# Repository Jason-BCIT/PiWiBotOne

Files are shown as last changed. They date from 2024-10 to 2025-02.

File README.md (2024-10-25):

The PiWiBot is a small, mobile, educational robot using the Raspberry Pi Pico microcontroller board.
The original code and inspiration for the software was developed and shared by Adrian Cruceru as "crawlspacebot". https://github.com/AdrianCX/crawlspacebot 

The printed circuit board is available from PCBWAY at https://www.pcbway.com/project/shareproject/PiWiBot_One_51645550.html 
Or you can manufacture your own, single sided board using the files included here.

To see two PiWiBots playing: https://youtu.be/jH2G25Dmx2Y  

To view the CAD in native Fusion 360 format: https://a360.co/40o5nz3 

The board is compatible with the "Tethered Mini Sumo" project.. a common "Tech Studies" project in British Columbia. https://botshop.wordpress.com/2011/03/30/tethered-mini-sumo-robots/ 
The entire robot, as presented here, can be manufactured for approximately $20CAD (batteries not included!) as of October 2024

To install the software, install Thonny on your computer and use it to copy the MicroPython image to your Raspberry Pi Pico W, using the instructions here: https://projects.raspberrypi.org/en/projects/getting-started-with-the-pico/2 

Copy the code in the Code folder to a folder on your computer. Open the code in Thonny, and then save to the Pico W.

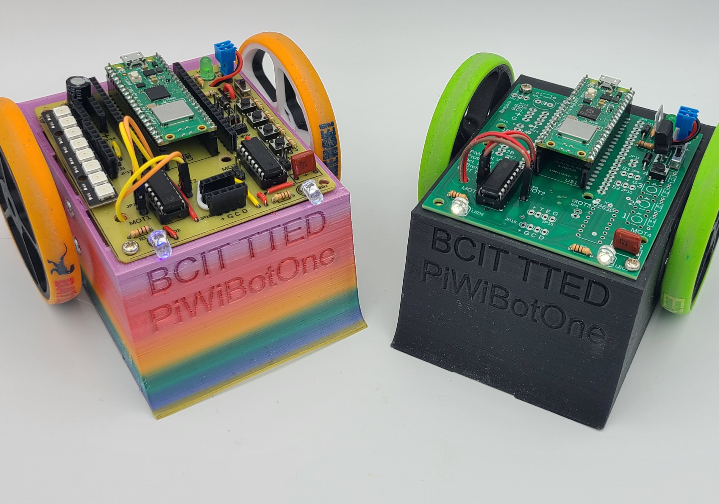
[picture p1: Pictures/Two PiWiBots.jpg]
Two PiWiBots


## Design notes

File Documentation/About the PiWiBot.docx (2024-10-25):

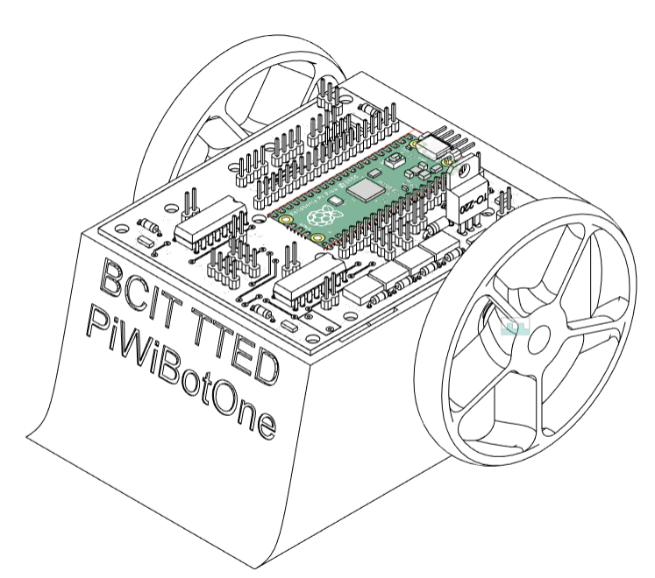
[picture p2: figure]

The $20 PiWiBot

(Raspberry Pi Pico Wireless Robot)

John Pinto wanted to make his tethered mini sumo robots wireless… for $20 or less (batteries not included.) The $8.00 Raspberry Pi Pico W board made this possible!

Contact: Jason Brett jbrett@bcit.ca

Give it a try!

PiWiBot Minimal Parts List | Vendor | Price
Raspberry Pi Pico W | Canakit | $8.00
L293D Motor driver | Amazon | $1.00
2 x TT Motor Gearbox | Amazon | $3.50
1 SPDT Slide Switch | Amazon | $0.13
3 x LEDs | Any | $0.30
2 x Rectifier Diodes | Any | $0.20
4 x resistors (2x100, 470,10K) | Any | $0.04
2 x 20pin header sockets | Lee’s | $0.90
2 x 40pin header pins | Lee’s | $1.00
1 x 180nF (approx.) cap | Any | $0.30
2 x Silicone Wrist Bands | Amazon | $1.00
113g PLA filament | Any | $2.60
1 x 4AA Battery Pack | Lee’s | $1.00
2 x Nut Inserts for 3D prints | Amazon | $0.25
2 x 3mm x 6mm screws | Any | $0.25
1 x Printed Circuit Board | PCBWAY | $1.80
Total Entry Level Price | | $22.27

And, technically you could get rid of the headers, solder the Pico directly to the board, screw directly to the plastic and hit the $20 price point. (Batteries not included, of course!)

1) Turn the switch (by the green power LED) ON.
2) Connect to:
  a. “PiWiBotOne” for the Rainbow Robot
  b. “PiWiBotTwo” for the Black Robot
  c. Password is “123456789”
  d. Navigate your browser to 192.168.4.1
3) Drive robot with left hand joystick. Use red corner buttons to control LEDs.
  a. The slider is for servo control, and the other joystick is for extra motors.
    i. The PiWiBot supports up to four DC motors and two servo motors.
4) The Rainbow bot has a 120:1 gearbox, the Black Robot has a 48:1 gearbox.
5) Remember to turn the robot off when done, please!

About the board:

1) The Rainbow bot’s board was made in the shop… good for one-off and prototypes
  a. The Black bot’s board was made by PCBWAY… $1.80 each in quantity of 100.
    i. Want to build a PiWiBot? Ask me for a sample board!
2) The code is mostly MicroPython, with Javascript and HTML used to create the web page.
  a. I’m happy to share… it is plug and play. (Mostly… but PC/Mac/Linux compatible)
  b. Lots of development left to go for additional accessories.
    i. Line following / edge detecting
    ii. Range finding with Ultrasonic or LIDAR rangefinders
    iii. OLED display on board
    iv. Speaker (apparently the Pico can play MP3 files… but I haven’t figured that out yet.)
    v. Multiple pushbuttons
    vi. Anything you want because you can add an expansion board using headers!
      1. I do plan to have a series of Youtube videos and explanations… one day.
3) You can power the robot using any 5V-12V battery. (I’m using 4xAA… Alkaline or NiMh)
4) This robot uses the “TT Motor Gearbox” but the Tamiya gearboxes will work fine, too.

This board is fully compatible with the standard tethered mini sumo robot project. It simply replaces the control board. It has two wires for the battery and two wires for each motor, just like the tethered board!

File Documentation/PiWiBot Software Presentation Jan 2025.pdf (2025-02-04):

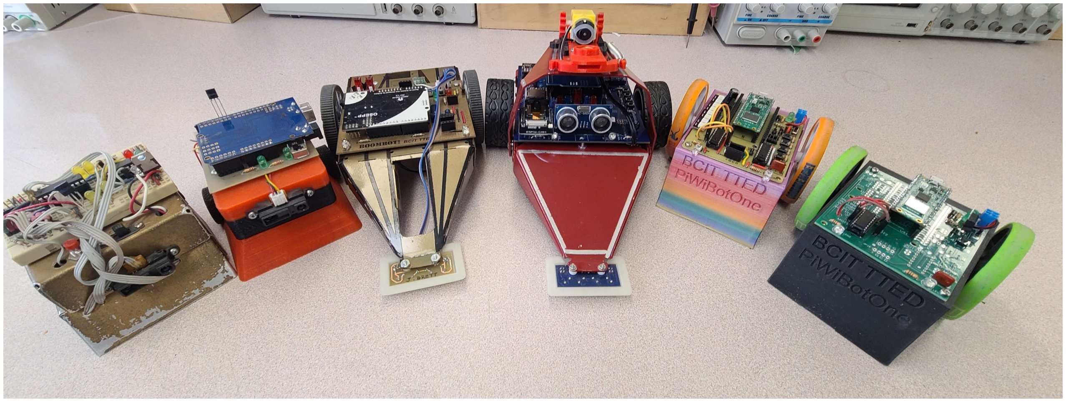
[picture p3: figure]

# PiWiBot Software

How I think it works.

Jason Brett
BCIT TTED
January 2025

# Coded in MicroPython

## - An Interpreted Language:

### - The PicoW doesn’t “run your code”

- It runs a “MicroPython Interpreter”

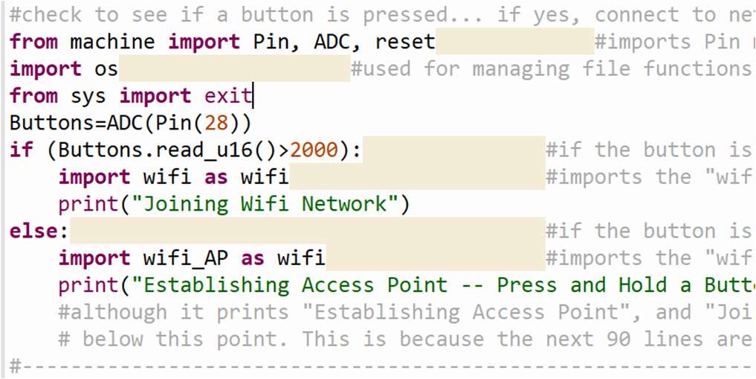
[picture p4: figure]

- Your source code is stored on the PicoW and executed one command at a time
- Use “Thonny” to install the MicroPython interpreter • Then to upload your code to the PicoW

## - On PicoW boot up the Micropython Interpreter starts to run

### - It looks for a file called “main.py”

- It executes the first instruction in that file
- Then the next, etc.

# Different from the Arduino IDE

## - Arduino IDE:

- Compiled language (“C++”) • Your computer converts your

source code to machine language instructions

### - The code on the microcontroller is in machine code

- You can’t read it or change it • You have to re-compile and re-

download

### - Benefit: Compiled code runs faster than interpreted

- (as a general rule)

## - Micropython:

- Interpreted language (“Python”) • Your microcontroller stores, reads

and executes source code

### - The code on the microcontroller is in source code

- You can edit and change it easily
- No need to re-compile or re-download

### - Benefit: Interpreted code can be easier to develop

- Faster chips compensate for slower code

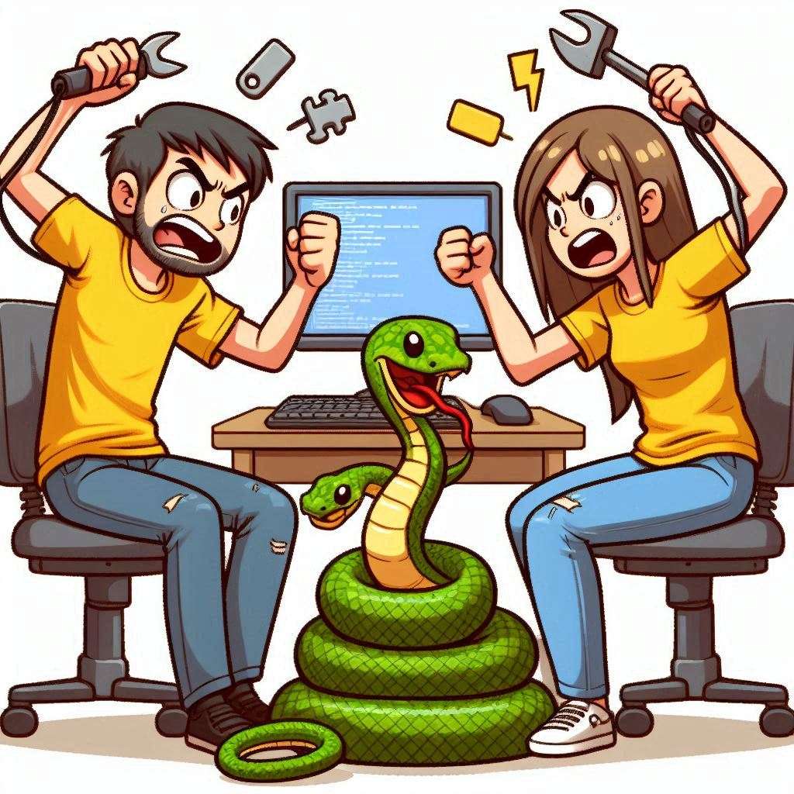
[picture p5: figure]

# Notable Syntax Differences

## - Python does not require semi-colons at end of line - Python does not use {loop} to manage loops

### - Loops are managed by indentations

- Indentation really, really matters!

## - Python’s comment code is “#” rather than “//” - “print()” includes the line feed and carriage return

### - “println()” not needed

## - Python offers several benefits when managing data

### - Not so important in this application but can reduce coding time

“A cartoon image of two computer programmers, one male, one female, fighting with a Python.” Generated by Microsoft CoPilot, Feb 2025

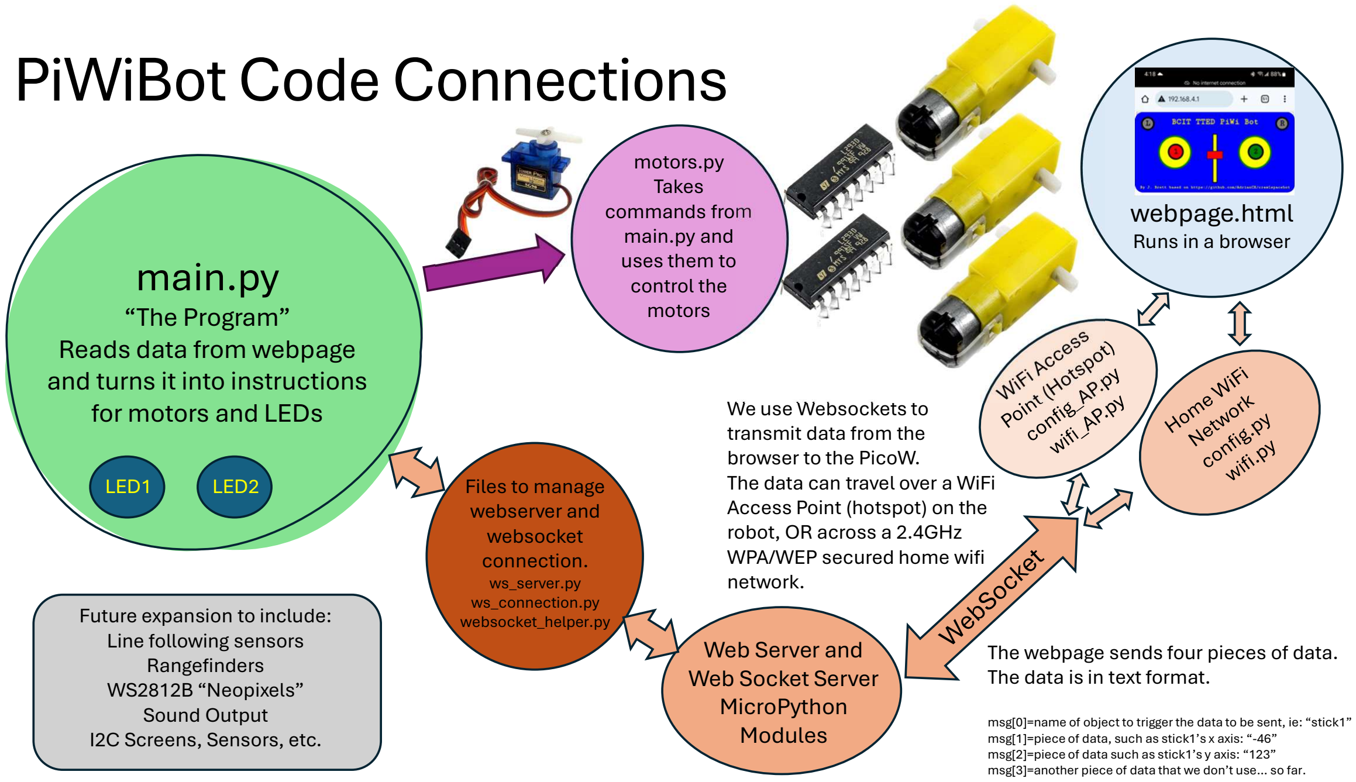
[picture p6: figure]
PiWiBot Code Connections; webpage.html Runs in a browser; Web Server and Web Socket Server MicroPython Modules; We use Websockets to transmit data from the browser to the PicoW. The data can travel over a WiFi Access Point (hotspot) on the robot, OR across a 2.4GHz WPA/WEP secured home wifi network.; The webpage sends four pieces of data. The data is in text format.; Files to manage webserver and websocket connection. ws_server.py ws_connection.py websocket_helper.py; main.py; “The Program” Reads data from webpage and turns it into instructions for motors and LEDs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

msg[0]=name of object to trigger the data to be sent, ie: “stick1” msg[1]=piece of data, such as stick1’s x axis: “-46” msg[2]=piece of data such as stick1’s y axis: “123” msg[3]=another piece of data that we don’t use… so far.

# Change WiFi Details

## - Config.py

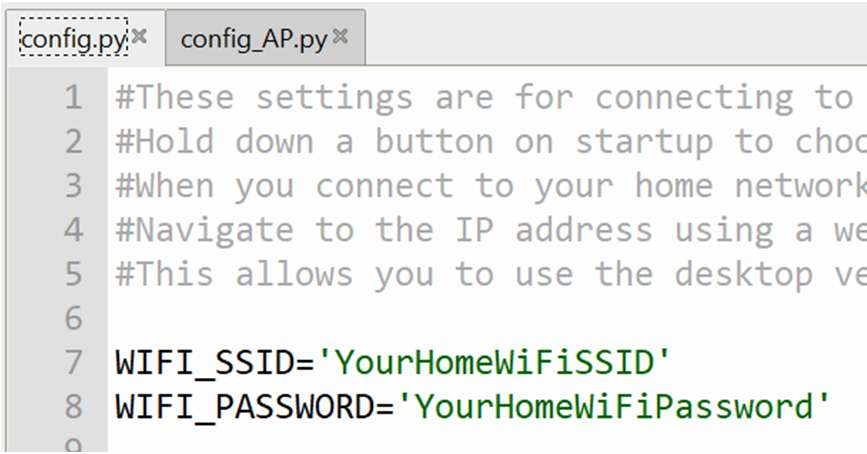
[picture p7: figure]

### - The SSID and Password for connecting to your home network - Hold down “the button” on the board on startup to connect

## - Config_AP.py

- Change the name of your robot’s network Access Point • Seriously, DO this… we don’t want six robot APs all named “PiWiBot”! • Add a password if you want.

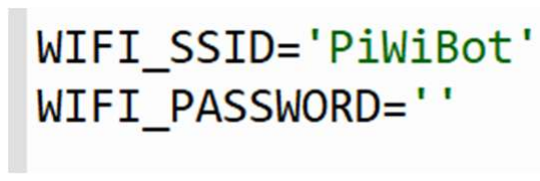
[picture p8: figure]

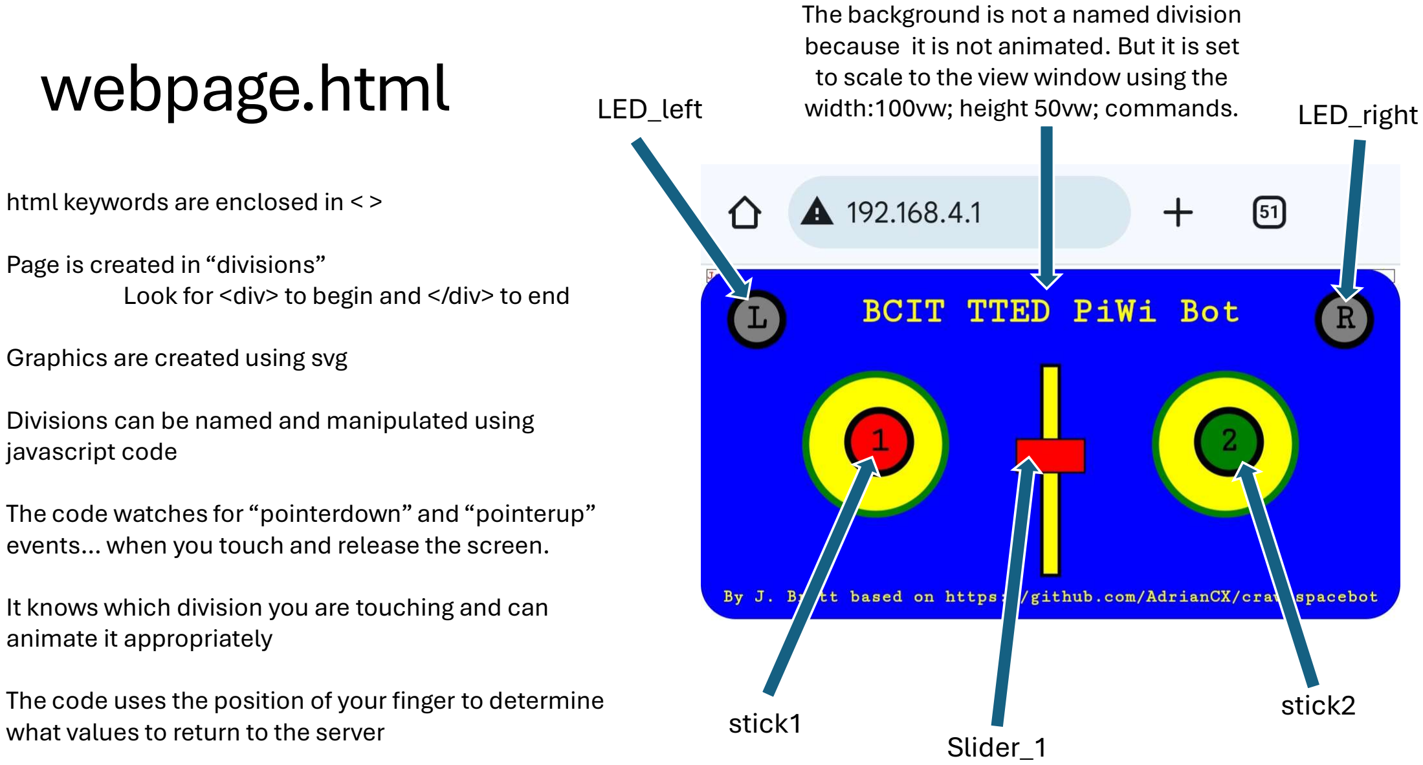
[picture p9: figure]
webpage.html; html keywords are enclosed in < >; Page is created in “divisions”; Graphics are created using svg; javascript code; animate it appropriately; what values to return to the server; LED_left; LED_right; stick1; stick2; Slider_1; The background is not a named division; to scale to the view window using the width:100vw; height 50vw; commands.

Look for <div> to begin and </div> to end

Divisions can be named and manipulated using

The code watches for “pointerdown” and “pointerup” events… when you touch and release the screen.

It knows which division you are touching and can

The code uses the position of your finger to determine because it is not animated. But it is set

# What Can I Hack?

## - Lots of easy stuff to change:

- Look for things between quotes… fill=“blue”, or r=“40”
- Look for text between <text> and </text> commands
- <text x="200" y="190" font-size="10" text-anchor="middle" fill="Yellow">By J. Brett based on https://github.com/AdrianCX/crawlspacebot</text>

## - A bit trickier, but you can remove unused objects

- Save a “webpage.backup” file in case you need to go back to step one!
- Delete the section from <div id=“stick2” to the next </div>
- At the end of the file delete the “let joystick2= ….,16); • Do the same for Slider1 if you don’t need it • Now can you re-centre joystick 1 to the middle of the screen?

## - Maybe you want one joystick with two sliders?

# How Does the Joystick Work?

- let joystick1 = new JoystickController("stick1", 128, 16); • Creates a new Joystick object • Names it “stick1”
- Associates it with the “stick1” division graphics
- The round button… it will animate this button as you move your thumb
- Creates a maximum range of movement of 128 drawing units
- Creates a “deadband” of 16 drawing units
- When either X or Y is less than 16 units from centre, it sets it to zero
- Makes it easier to re-centre the stick, and prevents accidental bumps

### - I was completely stuck on how to do this until I found

- “CrawlSpaceBot” by Adrian Cruceru on Github
- I’ve figured most of it out, but not all of it…. yet.

Y= -128

Y= +128

X= -128 | X= +128 Dead
Band

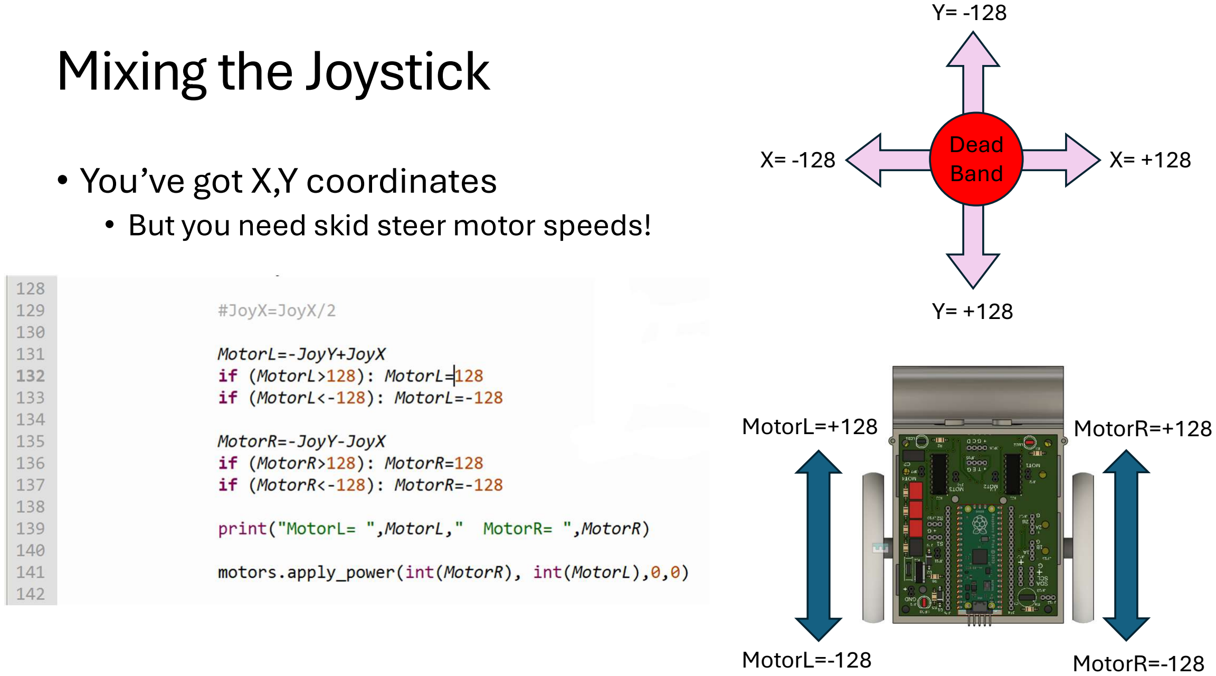
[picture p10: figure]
Mixing the Joystick; • You’ve got X,Y coordinates • But you need skid steer motor speeds!; X= +128 Dead; Band; MotorL=+128; MotorL=-128; MotorR=+128; MotorR=-128

# Driving the Motors

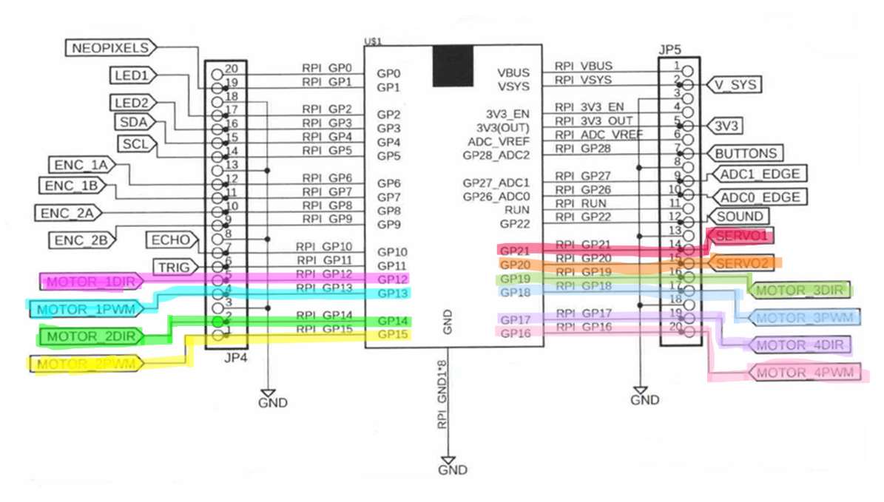
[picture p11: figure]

## - Wiring Determined by Schematic - Each motor has

### - 1 “DIR” pin to set direction - 1 “PWM” pin to set speed

- If decreasing the duty cycle makes the motor speed up going forward (DIR=HIGH) • Then increasing the duty cycle makes the motor speed up going in reverse (DIR=LOW)

## - Pico has many PWM options

- Set the frequency (how often it turns on and off) • We use a default of 5000Hz… you can sometimes hear a 5000Hz whining! • Set the duty cycle (the fraction of the time that it is turned “on”) • This is a fraction of a 16 bit number… 0 is “always off”, 65,535 is “always on”
- The Arduino only has an 8 bit “analogWrite”… at 980Hz

# Motors Need a Kickstart

## - The friction on the gearbox requires a minimum torque to turn

### - Below this the motor is stalled - The code uses a PWM setting of 25,000/65,536 = 38% to start up

- The code scales the motor response from 38% at low throttle to 100% at full throttle

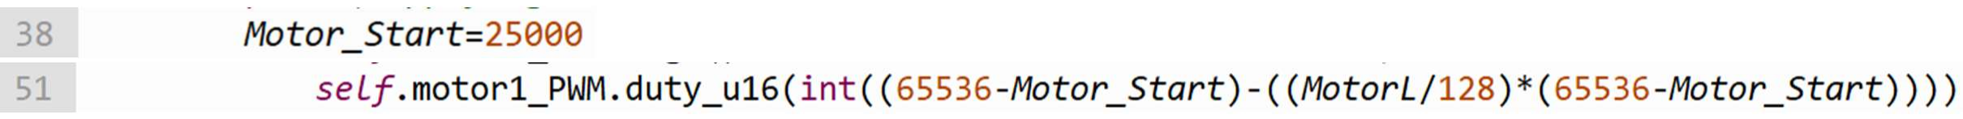
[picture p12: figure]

## - Often motors are “reversed”

### - Direction can be changed by swapping the wires on the board, or - Swapping a “+” to a “-” in code

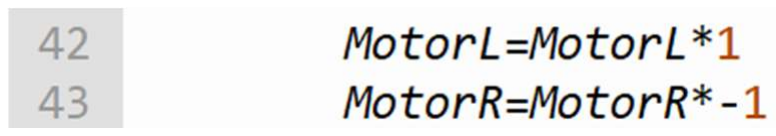
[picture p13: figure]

# Motor3 is On Slider1

### - You can slide the slider to position and leave it there

- You can take your thumb
off the controller and
Motor3 keeps moving
- It’s “return to zero”
function has been turned
off in the webpage
javascript code
- It won’t stop when you stop the code from Thonny
- You’ll need to add some
lines to shut the motor
down automatically
- Look at lines 168-174 in main.py

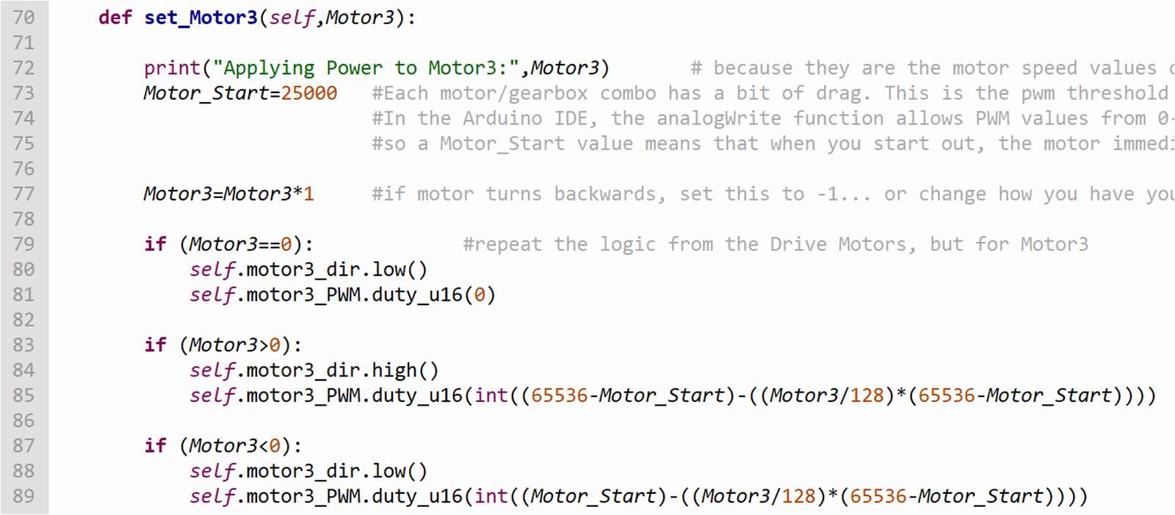
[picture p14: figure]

# Servo1 Uses Joystick2’s Y-Axis

## - We use a 50Hz PWM signal to send a pulse every 20ms

### - Servos will turn off if they don’t receive regular updates

## - Typical pulse lengths for a “hobby servo” are 1000-2000ms

- Neutral position is 1500ms (angle=0) • Positions range from +128 to -128 in our code

### - We set the duty cycle using nanoseconds

- 1500ms = 1,500,000ns

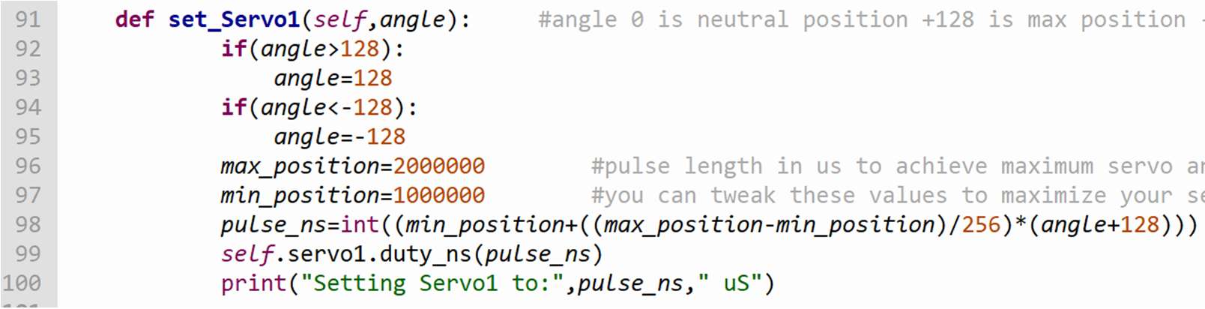
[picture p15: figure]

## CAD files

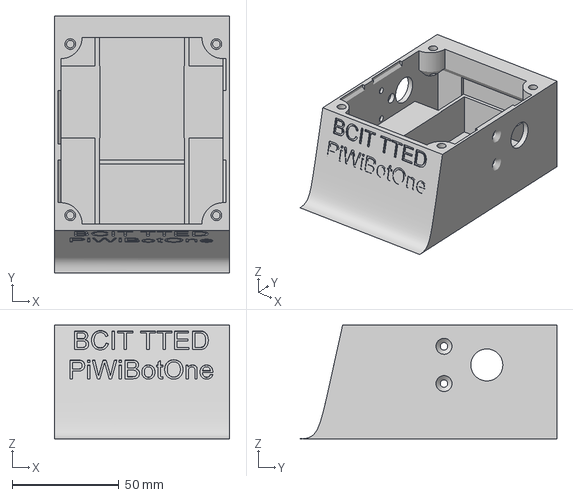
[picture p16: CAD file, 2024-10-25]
3D Print Files for Chassis and Wheel/PiWiBotOne ChassisV2.3mf
82.2 x 120.6 x 53.4 mm

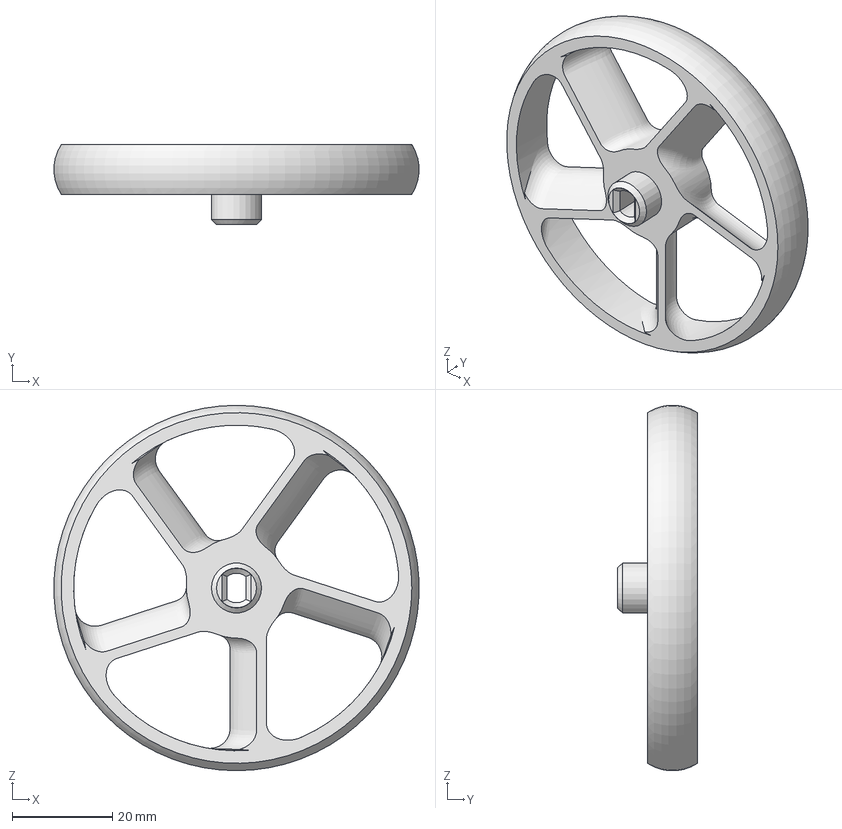
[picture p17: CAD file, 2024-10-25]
3D Print Files for Chassis and Wheel/70mm wheel for wristbands.3mf
72.9 x 16.0 x 72.9 mm

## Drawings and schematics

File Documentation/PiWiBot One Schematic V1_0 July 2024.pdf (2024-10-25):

# PiWi Bot Max V1.0 J. Brett

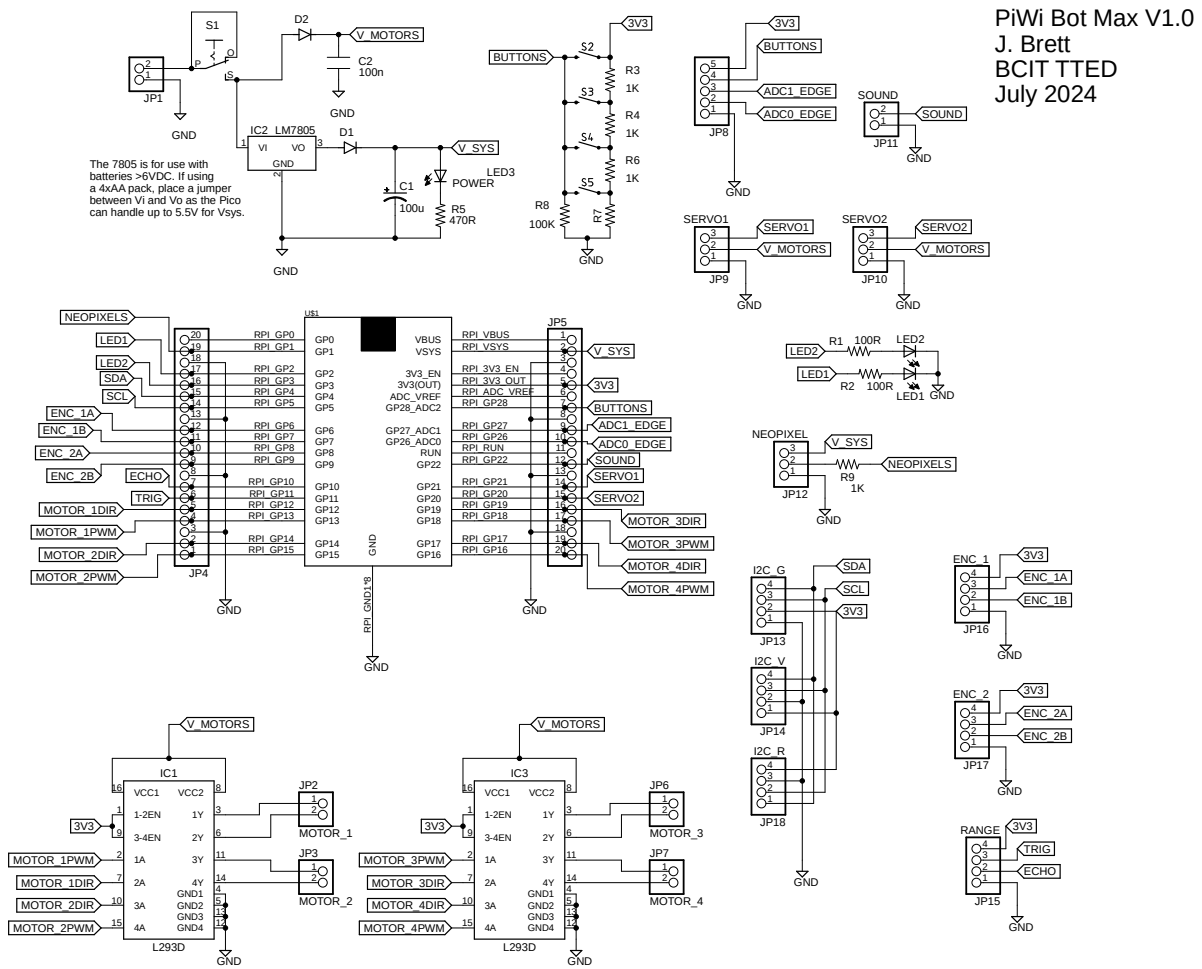
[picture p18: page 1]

The 7805 is for use with
batteries >6VDC. If using
a 4xAA pack, place a jumper
between Vi and Vo as the Pico
can handle up to 5.5V for Vsys.

15 | 6
14 | 7 | BUTTONS

12 | SOUND

TRIG | SERVO2

6 | | 15
5 | | 16
4 | | 17
3 | | 18

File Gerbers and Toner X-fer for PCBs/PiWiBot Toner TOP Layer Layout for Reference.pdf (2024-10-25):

## SCL

## SDA

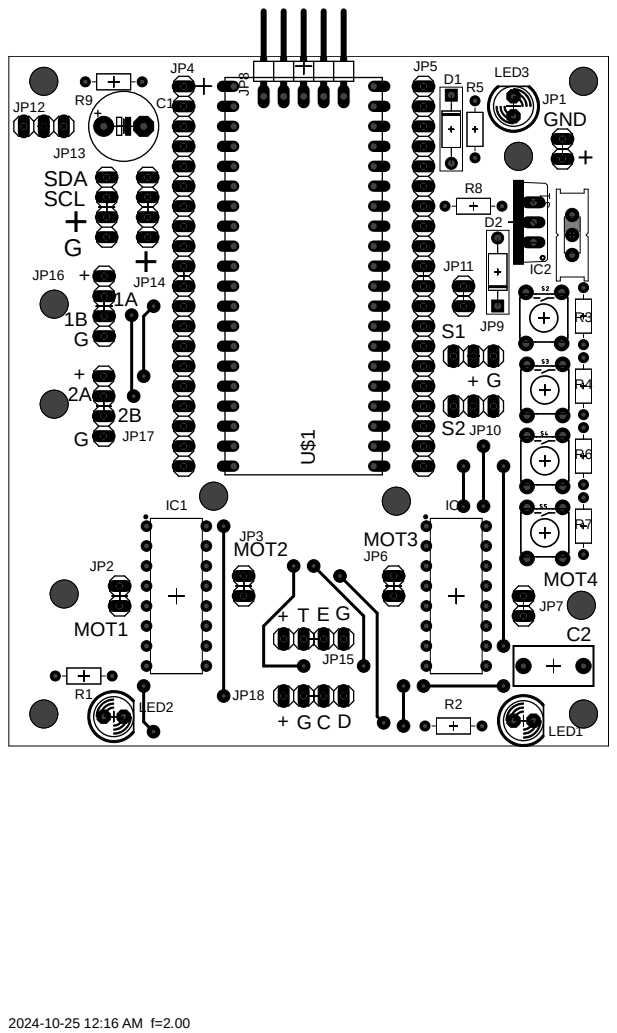
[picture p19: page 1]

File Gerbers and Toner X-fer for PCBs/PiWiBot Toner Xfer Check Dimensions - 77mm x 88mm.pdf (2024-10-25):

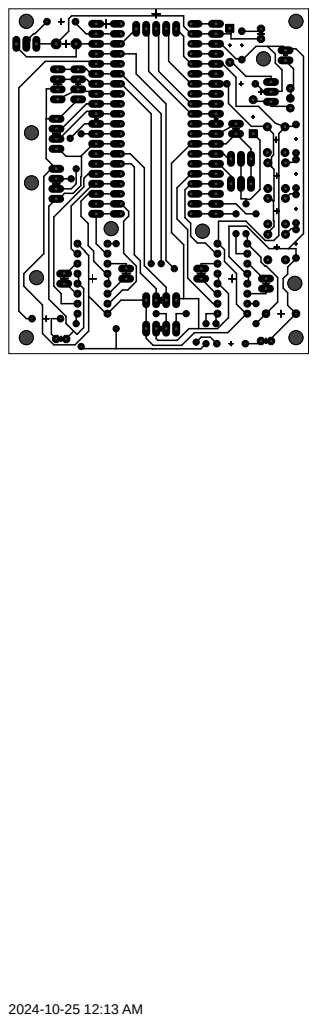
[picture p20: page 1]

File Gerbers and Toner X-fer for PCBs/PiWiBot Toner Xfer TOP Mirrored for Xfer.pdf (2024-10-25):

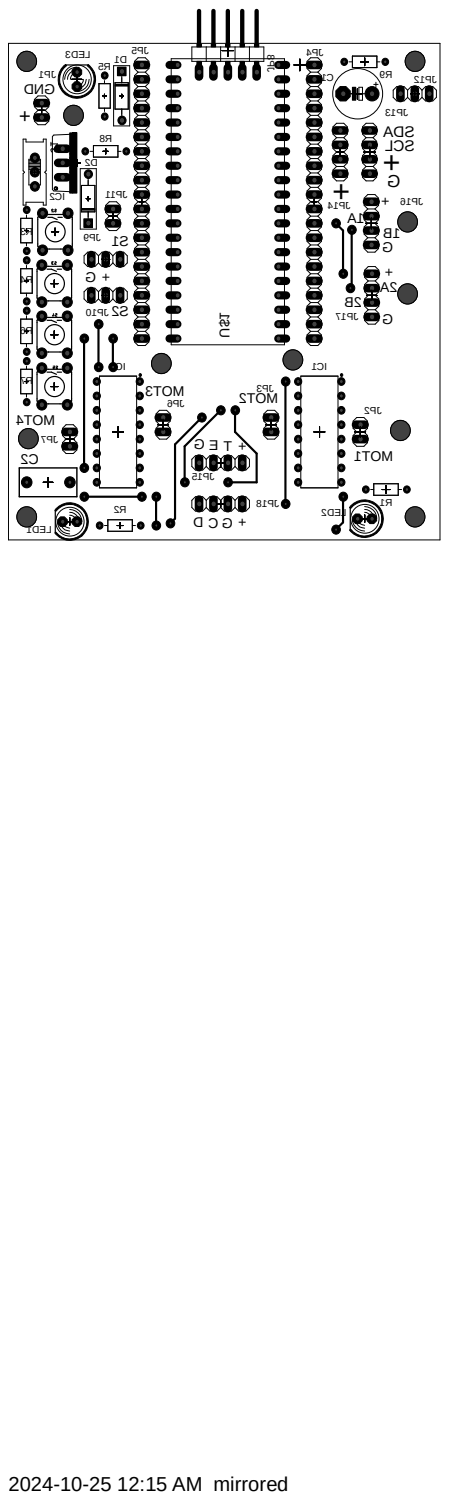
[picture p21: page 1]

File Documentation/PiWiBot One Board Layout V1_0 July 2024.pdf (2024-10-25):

## Edge Detector

## SCL

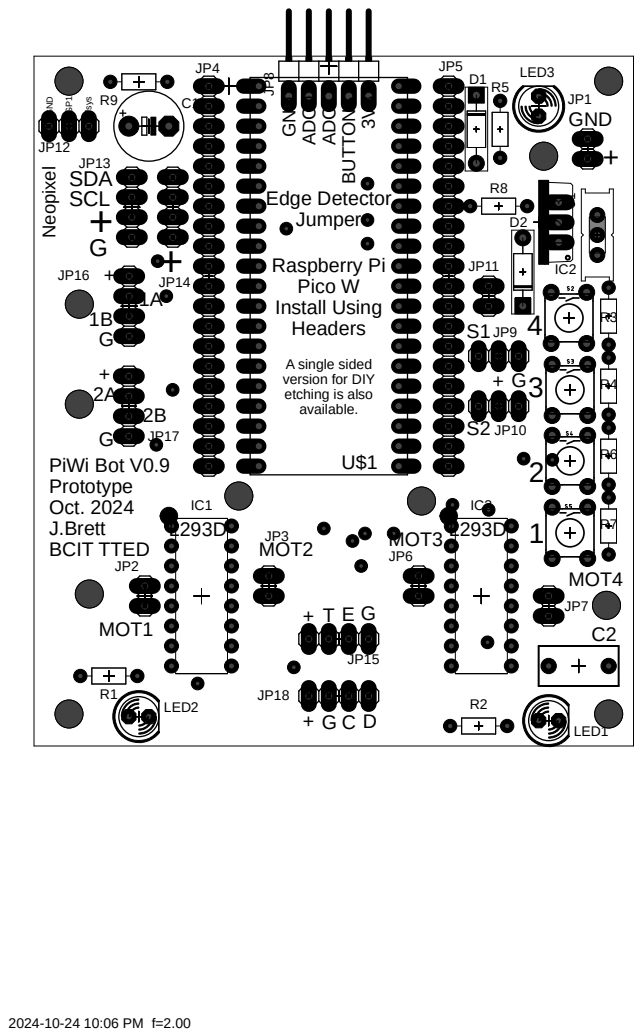
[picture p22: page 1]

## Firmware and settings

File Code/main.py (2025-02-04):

#This program executes upon startup. It is the main program that calls all the other functions for running the PiWiBot
#When running PiWiBot code from Thonny, this is the program that you need to run!

#The code for this project is located at: https://github.com/Jason-BCIT/PiWiBotOne    Check there for updates and feel free to fork/copy all you want.
#This code is based on "CrawlSpaceBot" by Adrian Cruceru, at https://github.com/AdrianCX/crawlspacebot   Published under MIT License (see license.py for details)

print("---------------------")
print("STARTING PiWiBot Code")
print("---------------------")

#------------------------------------------------------------------------------------------------------------------------------------------
#check to see if a button is pressed... if yes, connect to network defined in wifi.py, else establish Access Point defined in wifi_AP.py
from machine import Pin, ADC, reset				#imports Pin mapping (which pin to which number) and Analog Digital Convertor functions from the MicroPython machine module (a module in micropython is like a library in the Arduino IDE)
import os					#used for managing file functions and creating a debugging file on the pico
from sys import exit
Buttons=ADC(Pin(28))
if (Buttons.read_u16()>2000):				#if the button is pressed when this code executes (once, at startup) it will force the robot to connect to your home network
    import wifi as wifi						#imports the "wifi.py" file from this package and names it wifi. This gives the parameters for connecting to your home network.
    print("Joining Wifi Network")
else:										#if the button is not pressed the robot will establish a WiFi access point. This is the default setting
    import wifi_AP as wifi					#imports the "wifi_AP.py" file from this package and names it wifi. This gives the parameters for establishing an access point.
    print("Establishing Access Point -- Press and Hold a Button on Startup to Join a home Network")
    #although it prints "Establishing Access Point", and "Joining Wifi Newtork" in this section of code, the actual setup of the AP or joining of the home network doesn't happen until you hit the wifi.run() command, about 90 lines
    # below this point. This is because the next 90 lines are used for setting up the functions that will be called by the main loop of the program. So if you're following the code step-by-step... jump ahead to where it says "wifi.run()"
#-------------------------------------------------------------------------------------------------------------------------------------------

import time										#a micropython library to manage time functions
import drive_motors								#the "drive_motors.py" file that is part of this package. It contains the instructions for setting up the motors and making them run.

from ws_connection import ClientClosedError				#imports the ClientClosedError function from the "ws_connection.py" file contained in this package
from ws_server import WebSocketServer, WebSocketClient	#imports two functions from the "ws_server.py" file contained in this package

LED_left = Pin(2, mode=Pin.OUT, value=1)			#The Left Hand "Headlight" is connected to pin 2, is an OUTPUT, and starts out turned ON
LED_right = Pin(3, mode=Pin.OUT, value=1)			#The Right Hand "Headlight" also starts out turned on, as the value is set to one

fileNumber=0

for x in range(1,5):				#five little flashes to confirm the code has started
    LED_right.value(0)				#only runs once, on startup
    time.sleep(0.1)
    LED_right.value(1)
    time.sleep(0.1)
    print("Boombot is Waking Up!")

motors = drive_motors.Motors()						#creates a motors object for the two drive motors. Refers to the "drive_motors.py" file, imported above
deadline = time.ticks_add(time.ticks_ms(), 300)		#reads the system clock and creates a deadline for 300 ms in the future. This is used to stop the robot if it loses communication with the controller

#if you're following the order of execution of this program, it now jumps all the way down to the wifi.run statement near the bottom of this file. Then it begins the infinite "while True" loop which runs the robot
#the infinite loop continuously calls the "server.process_all" function which is defined towards the end of the "ws_server.py" file. It then refers the program execution back to the process function, defined below

def manage_file (mode):                #if mode=1 then search for a safe filename and open a new file, if mode=0 then close the file
    global fileNumber                #creating and opening the new file can take many 10's of ms, longer when searching for a unique filename
    global f
    global fileName
    
    if (mode==1):										#manage_file(1) creates a new log file
        fileName="DriveLog"+str(fileNumber)+".txt"       #this line creates a log file on the PicoW and overwrites the previous log file    
        #exists=False									#if you want to maintain a unique log file for each power up sequence, uncomment this code
        #while (exists==False):							#it will check to see if the file name you are creating already exists, and if it does
        #    try:										#then it will increment the file number by one and try again
        #       f = open(fileName, "x")					#just keep in mind that it will eventually fill up the PicoW's storage with log files
        #       exists = True							#so if you do uncomment this, remember to clean out the log files every few dozen runs
                
        #    except OSError:
        #       exists = False
        #        print(fileName," exists already")
        #        fileNumber=fileNumber+1
        #        fileName="Drive"+str(fileNumber)+".txt"
        
               
        f = open(fileName, "w")
        print(fileName)
        f.write("start driving\n")
        
    if (mode==0):									#manage_file(0) closes the existing log file
        f.write("All done. Controlled Exit from Code.")
        f.close()
    

class TestClient(WebSocketClient):					#this defines a class to manage the websocket communication with the javascript code (in webpage.html) that runs on the phone/tablet/PC controlling the robot
    def __init__(self, conn):						#the class refers to the WebSocketClient function that is imported from the "ws_server.py" file earlier in this program
        super().__init__(conn)						#this is some weird object-oriented programming stuff that I'm still trying to figure out... but it has to do with how the class is initialized when you first set it up

    def process(self):								#This function gets called repeatedly to check for data from the controller and set values based on what the data contains. It exists inside the TestClient class, defined above
        try:
            #"try" is Python's way to say, "do this, but if there is an error, break out of the command and report the error back so we can handle it"
            msg = self.connection.read()			#This tries to read the connection
            if not msg:
                f.write("-")			#if there is no readable message quickly record a "-"
                f.flush()
                return								#but if there is no data there, it ends the function and returns to wherever the function was called from
            msg = msg.decode("utf-8")				#this interprets the data as a standard text file
            msg = msg.split("\n")[-2]				#this splits the data wherever a "new line" character is
            msg = msg.split(" ")					#this splits the data wherever a "space" character is
            
            #The data that is being split comes from the javascript running on the browser being used to drive the robot (see webpage.html)
            #The usual format will have the name of the object that created the data in the msg[0] field
            #For a joystick object the msg[1] field will contain the X value of the joystick and msg[2] will contain the Y value
            #For a slider the position of the slider will be reported in msg[1]
            #For an LED button, the desired value for the LED (1=HIGH, 0=LOW) will be in msg[1]
            
            deadline = time.ticks_add(time.ticks_ms(), 300)			#since data was successfully received (or we wouldn't be at this point in the code) extend the deadline for another 300ms
            print(msg[0]," X:",int(msg[1])," Y:",int(msg[2]))		#print the first three items of data received. The first item will be the name of the object that created the data... eg "stick1" or "LED_Left"
            try:
                f.write("Message Decode Time="+str(time.ticks_ms())+","+str(msg[0])+","+str(msg[1])+","+str(msg[2])+"\n")
                f.flush()
            except:
                print("Didn't record data")
                f.write("Didn't record data")
                f.flush()
                
            if msg[0]=="LED_Left":						#if the message came from the LED_Left object on the webpage
                LED_left.value(int(msg[1]))				#set the LED_left pin to the value of the next data element (expected to be 1 for HIGH and 0 for LOW)
                print("LED_left=",int(msg[1]))			#print the data over the serial monitor to help with debugging
            
            if msg[0]=="LED_Right":						#see LED_Left, above, for explanation
                LED_right.value(int(msg[1]))
                print("LED_right=",int(msg[1]))
                
            if msg[0]=="stick1":						#if the message came from the "stick1" object then we will mix the X and Y values and use them to control the robot's motors
                JoyY=int(msg[2])						#the data comes from the webpage as characters, so we use the "int" statement to turn it into an integer variable so that we can do math with it
                if ((JoyY<5) and (JoyY>-5)):  			#this is the "deadband". It means that the joystick doesn't have to be perfectly centered in order for the motors to turn off
                    JoyY=0								#so if the joystick is "close" to centre then just set it to zero. Want a bigger deadband? Increase the value in the previous line (default=5)
                    
                JoyX=int(msg[1])						#see the JoyY section, above, for explanation
                if ((JoyX<5) and (JoyX>-5)):  			#deadband
                    JoyX=0
                
                JoyX=JoyX/2							#if your robot's turning is too sensitive, you can dampen the turn response by reducing the value of JoyX. Uncomment this command to cut the sensitivity in half
                
                MotorL=-JoyY+JoyX						#these lines "mix" the JoyX and JoyY values to create the speeds for each motor. For more details google "Joystick mixing for arcade drive"
                if (MotorL>128): MotorL=128				#the motor's speed settings range from -128 (full reverse) to +128 (full forward). Zero is "stop".
                if (MotorL<-128): MotorL=-128			#these two statements make sure that the speed never exceeds these limits
                
                MotorR=-JoyY-JoyX						#these lines create the speed value for the right motor using a similar technique to the left motor, above
                if (MotorR>128): MotorR=128
                if (MotorR<-128): MotorR=-128
                
                print("MotorL= ",MotorL,"  MotorR= ",MotorR)		#print out the values for debugging
                      
                motors.apply_power(int(MotorR), int(MotorL),0,0)    #send the values to the motors.apply_power function (located in the "drive_motors.py" file)
                                                                    #it is possible to send four values to the motors.apply_power function, so future expansion to four drive motors is possible
            if msg[0]=="Slider_1":
                slider=int(msg[2])					#convert the slider message to an integer number
                if ((slider<15) and (slider>-15)):  			#this is the "deadband". It means that the slider doesn't have to be perfectly centered in order for the motors to turn off
                    slider=0
                if (slider>128): slider=128				#the motor's speed settings range from -128 (full reverse) to +128 (full forward). Zero is "stop".
                if (slider<-128): slider=-128			#these two statements make sure that the speed never exceeds these limits
                print("Slider1= ",slider)
                motors.set_Motor3(slider)
            
            if msg[0]=="stick2":
                motors.set_Servo1(int(msg[1]))


        except ClientClosedError:					#at the beginning of this function there is a "try" command. In the event that an error occurs during the function, it will come here to handle common errors
            print("Connection close error")			#the connection to the webpage was closed. Perhaps the browser was closed?
            self.connection.close()					#close the connection
            #cleanup GPIO settings here
            motors.apply_power(0,0,0,0)				#stop the motors
            f.write("ClientClosedError\n")
            f.flush
        #except e:									#this is some MicroPython error catching code that I'm still figuring out. You can ask me about it, but as of Jan. 2025 my answer will be "I don't know."
        #    print("exception:" + str(e) + "\n")		#thankfully it doesn't matter that much as it only executes if there is an error
        #   #cleanup GPIO settings here
        #    motors.apply_power(0,0,0,0)				#stop the motors
        #    raise e									#Hmm... I really don't know what I'm doing with this code. This is one of the lines I "just copied". I think this logs an error to the log file. Maybe. Or something...
        except KeyboardInterrupt:					#this will trigger if you send a command from Thonny to stop program execution
            print("Keyboard interrupt over serial connection.")
            f.write("\nKeyboard interrupt over serial connection. \n")
            f.flush()
            motors.apply_power(0,0,0,0)				#stop the motors
            f.close()
            sys.quit()
            
        except:
            motors.apply_power(0,0,0,0)			#if an error occurred in the preceeding try, and it wasn't a ClientClosedError (from the website) or a Keyboard Interrupt, then flash the LEDs and complain
            for x in range(1,10):
                LED_right.value(1)
                time.sleep(0.1)
                LED_right.value(0)
                time.sleep(0.1)
            print("An Error occurred in the main loop")
            f.write("An Error occured in the main loop\n")
            f.flush()
    
class TestServer(WebSocketServer):					#this defines the TestServer class and refers to the WebSocketServer class imported from the "ws_server.py" file in this package
    def __init__(self):								#this runs once, on initialization of an object of this class
        super().__init__("webpage.html", 100)		#and references the "webpage.html" file that will be served to the phone/tablet/PC browser that connects to the PiWiBot

    def _make_client(self, conn):					
        return TestClient(conn)
    
manage_file(1)		#create a log file for troubleshooting
wifi.run()			#depending on whether the button was pressed on startup, either the "wifi.py" file or the "wifi_AP.py" file will be imported and named "wifi"
                    # each of these files has a "run" function. To follow the code execution, take a look for the "run" function in either wifi.py or wifi_AP.py

server = TestServer()	#the class "TestServer" is defined, above. When this class is assigned to the name "server", the __init__ function will execute, so the code will jump to the "ws_server.py" file
server.start()			# the server object, created in the last command, has a function called "start". You can see the definition of this function in the "ws_server.py" file


while True:						#Infinite Loop! The indented code, below, will keep cycling around until you tell it to stop, or turn the robot's power off
    
    server.process_all()										#the "server" object was created about six lines above here. The "process_all" function is included in the file "ws_server.py"
    if time.ticks_diff(deadline, time.ticks_ms()) < 0:			#checks to see if the "deadline" time is less than the current time. If it is, then the deadline has passed and we have had a communications problem
        print("Data link not responding. Motors turned off.")	# if there is a communication problem, report the problem
        motors.apply_power(0,0,0,0)								# turn off the motors
        deadline = time.ticks_add(time.ticks_ms(), 10000)		# and create a longer deadline so that the PicoW and the control device have a chance to re-establish communication
            
server.stop()				#this code will execute should something happen to break out of the main loop. But it may never actually execute.

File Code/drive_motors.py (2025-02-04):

from machine import Pin, PWM		#This imports the Pin definitions and PWM routines from the MicroPython machine module (aka 'library')

#Each motor requires two pins. One controls speed (that's the PWM pin) and one controls the direction. 

class Motors():									#this creates a class for the motors. The class includes both the definition of which pins are for which motor, and the apply_power function to set the speeds of the two main drive motors
    def __init__(self):							#the __init__ function executes when an object of this class is created
        self.motor1_dir=Pin(12, mode=Pin.OUT)	#this sets motor1's direction pin to be on GPIO Pin 12 and assigns it as a High/Low OUTPUT (much like the pinMode command in the Arduino IDE)	DEFAULT VALUE is 12
        self.motor1_PWM=PWM(Pin(13))			#this sets motor1's speed pin to be on GPIO Pin 13, and sets it as a PWM output. This will allow for variable motor speeds.	DEFAULT VALUE is 13
        self.motor1_PWM.freq(5000)				#this sets the frequency of the PWM output to 5000Hz.
        self.motor1_PWM.duty_u16(00000)			#and this sets the duty cycle of the PWM output on the pin to 0... so the pin is always LOW to start.

        self.motor2_dir=Pin(14, mode=Pin.OUT) #Motor two works similar to motor1, above. Default Value is 14
        self.motor2_PWM=PWM(Pin(15)) #Default Value is 15
        self.motor2_PWM.freq(5000)
        self.motor2_PWM.duty_u16(00000)
        
        self.motor3_dir=Pin(19, mode=Pin.OUT) #Motor two works similar to motor1, above. Default Value is 19
        self.motor3_PWM=PWM(Pin(18)) #Default Value is 18
        self.motor3_PWM.freq(5000)
        self.motor3_PWM.duty_u16(00000)
        
        self.motor4_dir=Pin(17, mode=Pin.OUT) #Motor two works similar to motor1, above. Default Value is 17
        self.motor4_PWM=PWM(Pin(16)) #Default Value is 16
        self.motor4_PWM.freq(5000)
        self.motor4_PWM.duty_u16(00000)

        self.servo1=PWM(Pin(21))  #Default value is 21
        self.servo1.freq(50)		#send a signal every 20mS
        #self.servo1.duty_ns(1000000) #one million nanoseconds is one ms, the netral position for a servo
        self.servo1.duty_u16(4000)
        
        #self.servo2=PWM(Pin(20))  #Default value is 20

#When the program is running it will call motors.apply_power, and pass the following information to this function

    def apply_power(self, MotorL, MotorR, Motor3, Motor4): 						#self refers to the object itself... yeah, I don't really get it either, but the other four variables are passed from the function call and they make sense
        print("Applying Power ",MotorL," ",MotorR," ",Motor3," ",Motor4)		# because they are the motor speed values on a scale of -128(reverse) to +128(forward). Zero is "stop". Motor3 and Motor4 are for future expansion if needed.
        Motor_Start=25000	#Each motor/gearbox combo has a bit of drag. This is the pwm threshold where the motors actually get enough power to overcome inertia and begin to turn. Default is 25000, but feel free to tweak this.
                            #In the Arduino IDE, the analogWrite function allows PWM values from 0-255 because it is 8 bit resolution, but PWM on the PicoW has 16 bit resolution, so the range of values is 0-65,535.
                            #so a Motor_Start value means that when you start out, the motor immediately jumps to about 40% of "full speed" (25K/65K=40%). Anything less might not move because of the drag of the gearbox and motor bearings.
        
        MotorL=MotorL*1		#if motor turns backwards, set this to -1... or change how you have your motors plugged in!
        MotorR=MotorR*-1		#if motor turns backwards, set this to 1... or change how you have your motors plugged in!
        
        if (MotorL==0):							#if the motor setting is zero (full stop)
            self.motor1_dir.low()				#then set the direction pin LOW
            self.motor1_PWM.duty_u16(0)			#and the speed pin to always be LOW.... with both sides LOW, no current flows through the motor and the motor is off
            
        if (MotorL>0):							#if the motor is supposed to be moving forward
            self.motor1_dir.high()				#set the direction pin HIGH
            self.motor1_PWM.duty_u16(int((65536-Motor_Start)-((MotorL/128)*(65536-Motor_Start)))) #and then figure out how often to set the speed pin LOW. Since the motor runs when the direction pin is HIGH and the speed pin is LOW
                                                                                                    #you increase the speed of the motor by decreasing the duty cycle of the speed pin
        
        if (MotorL<0):							#if the motor is supposed to be moving in reverse
            self.motor1_dir.low()				#set the direction pin LOW
            self.motor1_PWM.duty_u16(int((Motor_Start)-((MotorL/128)*(65536-Motor_Start))))		#and then figure out how often to set the speed pin HIGH. In reverse the motor runs when the dir pin is LOW and the speed pin is HIGH
                                                                                                    #so to increase the speed of the motor you increase the duty cycle of the speed pin
        if (MotorR==0):				#repeat the logic for the Left Motor, but for the Right hand motor
            self.motor2_dir.low()
            self.motor2_PWM.duty_u16(0)
            
        if (MotorR>0):
            self.motor2_dir.high()
            self.motor2_PWM.duty_u16(int((65536-Motor_Start)-((MotorR/128)*(65536-Motor_Start))))
           
        if (MotorR<0):
            self.motor2_dir.low()
            self.motor2_PWM.duty_u16(int((Motor_Start)-((MotorR/128)*(65536-Motor_Start))))
            
    def set_Motor3(self,Motor3):
        
        print("Applying Power to Motor3:",Motor3)		# because they are the motor speed values on a scale of -128(reverse) to +128(forward). Zero is "stop". Motor3 and Motor4 are for future expansion if needed.
        Motor_Start=25000	#Each motor/gearbox combo has a bit of drag. This is the pwm threshold where the motors actually get enough power to overcome inertia and begin to turn. Default is 25000, but feel free to tweak this.
                            #In the Arduino IDE, the analogWrite function allows PWM values from 0-255 because it is 8 bit resolution, but PWM on the PicoW has 16 bit resolution, so the range of values is 0-65,535.
                            #so a Motor_Start value means that when you start out, the motor immediately jumps to about 40% of "full speed" (25K/65K=40%). Anything less might not move because of the drag of the gearbox and motor bearings.
        
        Motor3=Motor3*1		#if motor turns backwards, set this to -1... or change how you have your motors plugged in!
        
        if (Motor3==0):				#repeat the logic from the Drive Motors, but for Motor3
            self.motor3_dir.low()
            self.motor3_PWM.duty_u16(0)
            
        if (Motor3>0):
            self.motor3_dir.high()
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

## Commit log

2025-02-04 Delete Code/motors.py
    replaced by drive_motors.py
2025-02-04 Delete Code/tires.py
    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
2025-02-04 Delete Code/tires_original.py
    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
